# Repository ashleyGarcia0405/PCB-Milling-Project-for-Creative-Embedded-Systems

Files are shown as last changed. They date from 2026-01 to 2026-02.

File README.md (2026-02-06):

# PCB-Milling-Project-for-Creative-Embedded-Systems
Files and steps for completion of the PCB Milling Assignment

# Step 1: KiCAD PCB Layout

Please download the 555timerCES folder to begin this step of the assignemnt. 

To complete this step, you must arrange and route connections between the components of the 555 timer LED flasher circuit inside KiCAD's PCB editor. There are three tutorial videos for this section. The first move through the whole process in detail and also gives context for the layout process in reference to the milling and assembly portion of this assignment. The second video is much shorter and runs through the process with little explanation. It is meant to be watched after the first video and to be a reference as you're doing the assignment. The third is an optional tutorial on more flexible custom board outlines imported from the internet or made yourself in programs like Inkscape.

Detailed tutorial:

Video Title (https://www.youtube.com/watch?v=kU7-52KIdco)

NOTE: Please remember when you're doing your board layout to have your design fit well within the bounds of 152mm x 106mm (your design will most likely be much smaller than this, but just in case you're feeling experimental), which is the maximum size of the copper board you have to work with. 

Reference tutorial:

Video Title (https://www.youtube.com/watch?v=aDHYiCxRZ-c)

Additional tutorial for custom board outlines (SEE CORRECTION AFTER THIS VIDEO):

Video Title (https://www.youtube.com/watch?v=fYuy1Yf_eXA)

CORRECTION TO PREVIOUS VIDEO: I neglected to say that when you're importing you custom board outline .svg file, you must select the layer as "Edge.cuts" in the same pop-up window as you set the scaling. I left the layer as "User.drawings". Please see the image below on where to select the layer.

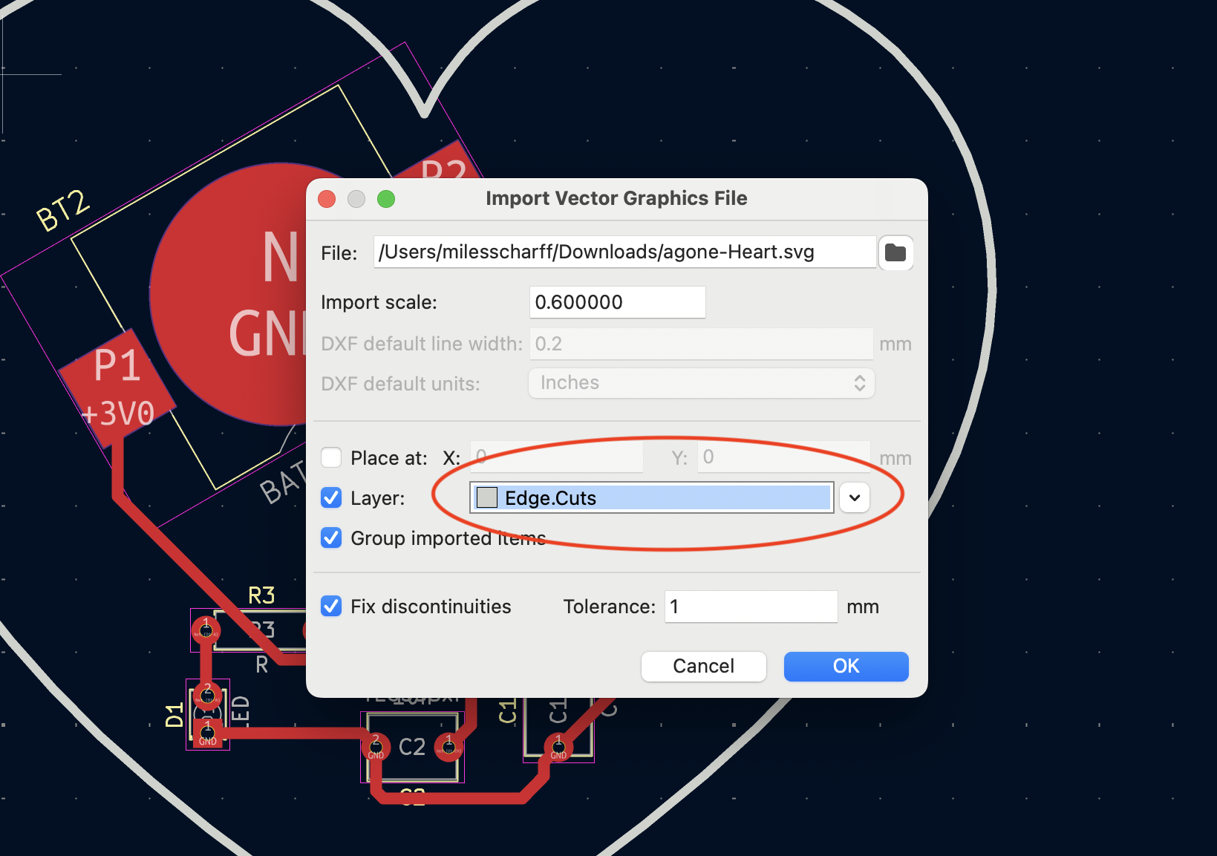
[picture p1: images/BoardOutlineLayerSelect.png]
BoardOutlineLayerSelect


# Step 2: Convert KiCAD Gerber and Drill Files to CNC Friendly SVGs

In this step, we will convert our gerber and drill files generated by KiCAD from out PCB layout into .svg files suitable for milling our PCB. We will use a shell script provided in this github called pcb_to_easel.sh to do this. I've provided a guide in this github as well, PCB_TO_EASEL_USE_GUIDE.md, that details the dependencies and what you need to alter in the shell script. Below is a video detailing the process of using the script. 

Video Title (https://www.youtube.com/watch?v=29JJRuPfXhc)

# Step 3: Mill Your PCB On The Carvey CNC

In this step, we use the .svg files we generated in Step 2 to mill our PCB on the Carvey CNC. It's important to note that there is no perfect way to do this process. Small physical initial conditions can change the result of your mill, and it's important to be able to adjust. In the tutorial video below, some of the results of my milling are unexpected, and I show how I respond and adapt to these results. The milling of your traces is most likely going to be the most likely going to take a few tries a different depths, as I show in the video. Also, I'm going to recommend that for your drill holes and your board outline that you utilize the "add depth" feature in Easel and add an additional 0.2mm up front. I show this in the video, though I end up adding the depth after an initial cut, and forget to do so when doing the drill holes. YOU MUST WATCH THIS TUTORIAL VIDEO AND UNDERSTAND THE PROCESS BEFORE YOU ATTEND YOUR CNC SESSION IN THE LAB.

Video Title (https://www.youtube.com/watch?v=hbWzbn1Lfh0)

# Step 4: Solder Components to Your Milled PCB

In the tutorial for this step, we choose component values to control our LED flashing frequency, and talk about techniques for soldering your components to your milled circuit board. Please note that due to voltage limitations of the CR2032 coin cell battery, we can only use red and yellow LEDs. Also we are using ceramic capacitors, NOT electrolytic. If you're confused what I mean, please refer to the two boxes in which I retrieve capacitors from in the video.

Video Title (https://www.youtube.com/watch?v=2ELSfMe3PyI)

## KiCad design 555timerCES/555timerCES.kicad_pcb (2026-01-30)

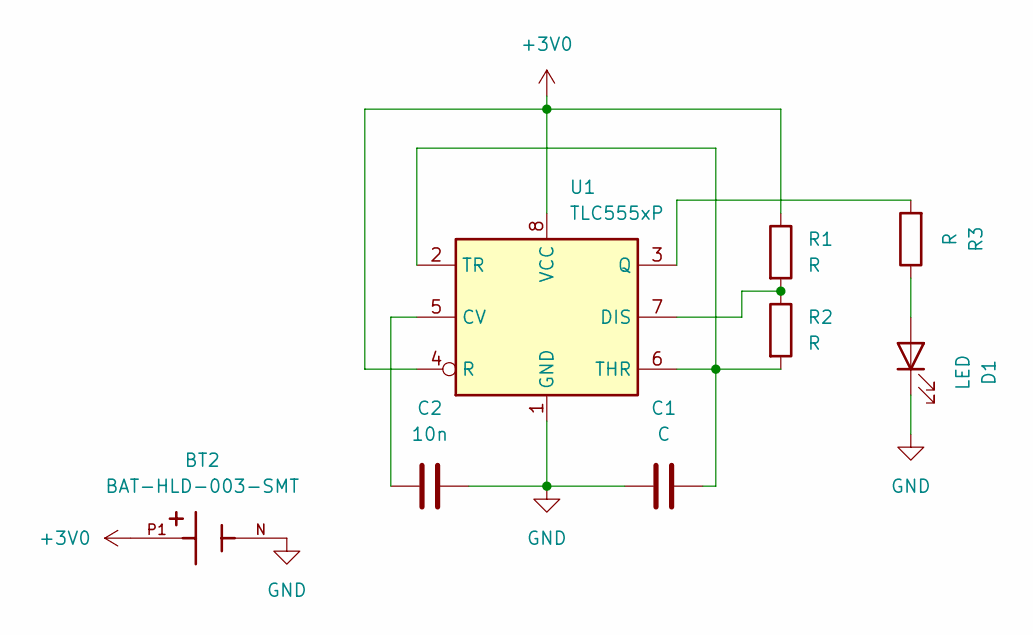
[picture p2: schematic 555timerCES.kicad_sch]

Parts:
BT2: BAT-HLD-003-SMT; BAT_BAT-HLD-003-SMT; DigiKey_Part_Number 343-BAT-HLD-003-SMT-ND
C1: C; C_Disc_D6.0mm_W4.4mm_P5.00mm
C2: 10n; C_Disc_D6.0mm_W4.4mm_P5.00mm
D1: LED; LED_D1.8mm_W3.3mm_H2.4mm
R1, R2, R3: R; R_Axial_DIN0207_L6.3mm_D2.5mm_P7.62mm_Horizontal
U1: TLC555xP; DIP-8_W7.62mm

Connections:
+3V0: BT2.P1, BT2.P2, R1.1, U1.4 (R), U1.8 (VCC)
GND: BT2.N, C1.1, C2.2, D1.1 (K), U1.1 (GND)
unnamed: D1.2 (A), R3.1
unnamed: C2.1, U1.5 (CV)
unnamed: R1.2, R2.1, U1.7 (DIS)
unnamed: R3.2, U1.3 (Q)
unnamed: C1.2, R2.2, U1.2 (TR), U1.6 (THR)

Board: 2 copper layers, 8 parts (0 on the bottom side), 7 nets, no tracks yet.

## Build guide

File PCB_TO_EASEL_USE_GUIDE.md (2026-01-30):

# KiCad PCB to Easel (Carvey CNC) Milling Guide

Convert KiCad PCB designs into SVG files for milling on a Carvey CNC using Easel.

## Table of Contents
1. [Overview](#overview)
2. [First-Time Setup](#first-time-setup)
3. [Quick Reference (Repeat Use)](#quick-reference-repeat-use)
4. [Troubleshooting](#troubleshooting)
4. [Command Line Example](#command-line-example)

## Overview

This workflow converts KiCad PCB designs to Easel-compatible SVGs using `pcb2gcode` for isolation routing calculations. The `pcb_to_easel.sh` script handles everything automatically.

**Pipeline:**
```
KiCad → Gerber/Drill Files → pcb2gcode → G-code → SVG → Easel
```

**Output Files:**
`simple_front.svg` Isolation milling paths for copper traces
`simple_drill.svg` Drill holes for components
`simple_outline.svg` Circuit board outline

## First-Time Setup

### 1. Install Homebrew (macOS package manager), skip if you already have this installed

Open Terminal and run:
```bash
/bin/bash -c "$(curl -fsSL https://raw.githubusercontent.com/Homebrew/install/HEAD/install.sh)"
```

After installation, run the commands it displays to add Homebrew to your PATH:
```bash
echo 'eval "$(/opt/homebrew/bin/brew shellenv)"' >> ~/.zprofile
eval "$(/opt/homebrew/bin/brew shellenv)"
```

### 2. Install pcb2gcode

```bash
brew install pcb2gcode
```

### 3. Verify Installation

```bash
pcb2gcode --version
```

You should see version information (e.g., `pcb2gcode 2.5.0`).

---

## Quick Reference (Repeat Use)

Once setup is complete, use these three steps for each PCB:

### Step 1: Export from KiCad

In KiCad PCB Editor:
1. **File → Plot**
   - Check **F.Cu** (front copper layer)
   - Check **Edge.Cuts** (board outline) — optional but recommended
   - Format: **Gerber**
   - Click **Plot**

2. **File → Fabrication Outputs → Drill Files**
   - Format: **Excellon**
   - Click **Generate Drill File**

You'll have these files in your project folder:
```
YourProject-F_Cu.gbr      # Copper traces
YourProject-Edge_Cuts.gbr # Board outline (optional)
YourProject-PTH.drl       # Drill holes
```
"YourProject" will be replaced by whatever your KiCAD project name is

NOTE: if you prefer to make your board outline in another software like Adobe Illustrator or Inkscape, that is okay, just omit edge cuts from this process. You will get a warning when you run the script that there is no edge cuts file, but don't worry about it. Just make sure you can export the shape of your board outline from whatever software you want to use as an SVG.

### Step 2: Configure & Run Script

1. Copy `pcb_to_easel.sh` to your KiCad project folder (or edit GERBER_DIR)

2. Edit the script to set your file names (lines 29-32):
   ```bash
   GERBER_DIR="$(dirname "$0")"  # Or set to your project path
   FRONT_CU="${GERBER_DIR}/YourProject-F_Cu.gbr"
   EDGE_CUTS="${GERBER_DIR}/YourProject-Edge_Cuts.gbr"
   DRILL_FILE="${GERBER_DIR}/YourProject-PTH.drl"
   ```
   Replace "YourProject" with whatever your KiCAD project name is (the name of your generated gerber and drill files)

   If you want to place pcb_to_easel.sh in a different diectory, set your own directory with something like GERBER_DIR="/Users/yourname/Documents/MyProject" 

   By default the milling diameter (MILL_DIA) is set to 0.24 and the isolation width (ISOLATION_WIDTH) is set to 0.8. These match the bit size and cut depth we use for isolation routing of our PCB traces and pads. To change these numbers would mean we would be using different CNC tooling or changing our cut depth when using V bits.

   There are many other parameters in the script that look as though they are editable and meaningful such as MILL_DEPTH, MILL_FEED, DRILL_SPEED, etc. These are placeholder values that are only there so we can use the pcb2gcode library, and have no impact on the actual milling process on the Carvey. Please do not edit any of these values. 

3. Run:
   ```bash
   chmod +x pcb_to_easel.sh   # First time only
   ./pcb_to_easel.sh
   ```
   this should have created a folder called `gcode/` in the path you set for GERBER_DIR containing svg files for your copper traces (`simple_front.svg`), drill holes (`simple_drill.svg`), and board outline (`simple_outline.svg`)

### Step 3: Import into Easel

See separate Easel tutorial for details

## Troubleshooting

If the script returns: "pcb2gcode: command not found"

Homebrew isn't in your PATH. Run:
```bash
eval "$(/opt/homebrew/bin/brew shellenv)"
```

If the script returns: "WARNING: file not found"

Check that:
- File names in script match your actual files (lines 29-31)
- You're running from the correct directory
- Files were exported from KiCad

If traces are too thin after milling

- Ensure Easel cut type is **"On Path"** (not "Outside")
- Check `MILL_DIA` matches your actual bit and milling depth (cut width changed based on depth when using a V bit)

If SVG won't import into Easel

The `simple_*.svg` files are ultra-simple. If import still fails:
1. Open in Inkscape
2. Save as "Plain SVG"
3. Try importing again

---

## Command Line Example

If you place pcb_to_easel.sh in your KiCAD directory

```bash
# 1. Navigate to your KiCad project
cd ~/path/to/your_KiCAD_project

# 2. Copy the script here (or edit GERBER_DIR in the script)
cp ~/path/to/pcb_to_easel.sh .

# 3. Edit the script to match your filenames
nano pcb_to_easel.sh
# Change lines 30-32 to your file names

# 4. Make executable (first time only)
chmod +x pcb_to_easel.sh

# 5. Run
./pcb_to_easel.sh

# 6. Check output
ls #Confirm the expected .svg files are there
```

If you place pcb_to_easel.sh somewhere else

```bash
# 1. Navigate to your KiCad project where your gerrber and drill files are
cd ~/path/to/your_KiCAD_project

# 2. Get full path
pwd #COPY THIS PATH

# 3. Navigate to wherever you placed the pcb_to_easel.sh script
cd
cd ~/path/to/pcb_to_easel.sh

# 4. Edit the script to match your filenames and replace GERBER_DIR with the path you copied from your KiCAD project directory
nano pcb_to_easel.sh
# Change lines 29-32 to your file names and file path

# 5. Make executable (first time only)
chmod +x pcb_to_easel.sh

# 6. Run
./pcb_to_easel.sh

# 7. Check output
cd
cd ~/path/to/your_KiCAD_project/gcode
ls #Confirm the expected .svg files are there
```

*Guide for KiCad → pcb_to_easel.sh → Easel/Carvey PCB milling workflow*
*Last updated: January 2026*

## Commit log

2026-01-29 Update README with PCB milling steps
    Added steps for PCB milling process.
2026-01-29 Embed YouTube video for PCB Milling Step 1
    Added an embedded YouTube video for Step 1 of the PCB Milling Assignment.
2026-01-30 Enhance README with KiCAD tutorial details
    Added detailed tutorial and reference video links for KiCAD PCB layout.
2026-01-30 Update PCB assignment README with additional tutorials
    Added a third tutorial video for custom board outlines and updated video links.
2026-01-30 Adjust image width for BoardOutlineLayerSelect
    Updated image width in README for clarity.
2026-01-31 Include note on maximum copper board size
    Added a note regarding board layout size constraints.
2026-02-01 Add Step 4 for soldering components to PCB
2026-02-03 Enhance PCB milling instructions in README
    Added detailed instructions for milling PCB on the Carvey CNC, including tips and recommendations based on personal experience.
2026-02-06 Update soldering tutorial in README
    Added detailed instructions for soldering components and component selection for LED flashing frequency.
